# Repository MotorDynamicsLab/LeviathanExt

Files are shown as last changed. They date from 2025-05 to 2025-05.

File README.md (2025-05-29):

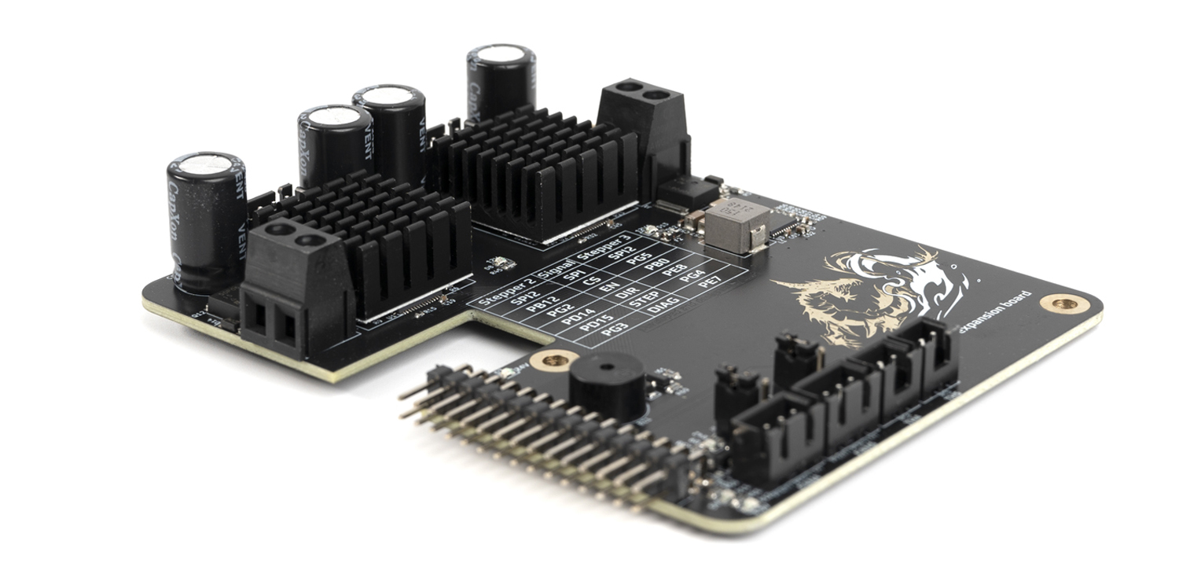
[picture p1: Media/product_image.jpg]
Leviathan_Ext Leviathan Extension


# Leviathan Extension Board

The Leviathan Extension Board is a plug and play PCB that expands the feature set of the original Leviathan controller board. It adds: 

- 2x Integrated TMC5160 stepper drivers. 
- 2x Fan ports with flyback protection, 12V/24V selectable voltage, and tachometer inputs. 
- 2x Thermistor ports with 2k2 ohm pullup resistors. 
- 1x Piezo Buzzer

## Electrical Specifications

| Parameter | Symbol | Min | Typ | Max | Unit | Comments |
| --- | --- | --- | --- | --- | ---- | --- |
| HV Stepper Supply Voltage | V<sub>HV</sub> | 24  | 48  | 55  | V | Supply voltage for the HV stepper drivers |
| Fan Current | I<sub>fan</sub> | | | 0.5 | A | Current rating per fan channel |
| HV Stepper Current | I<sub>hv_mot</sub> | | | 3 | A | Current rating of each TMC5160 stepper driver |

## Creating a Custom Extension PCB

Did you ever want to create your own custom extension board? We have a [template KiCad project](https://github.com/MotorDynamicsLab/Leviathan-Ext-Template) to help get you started.

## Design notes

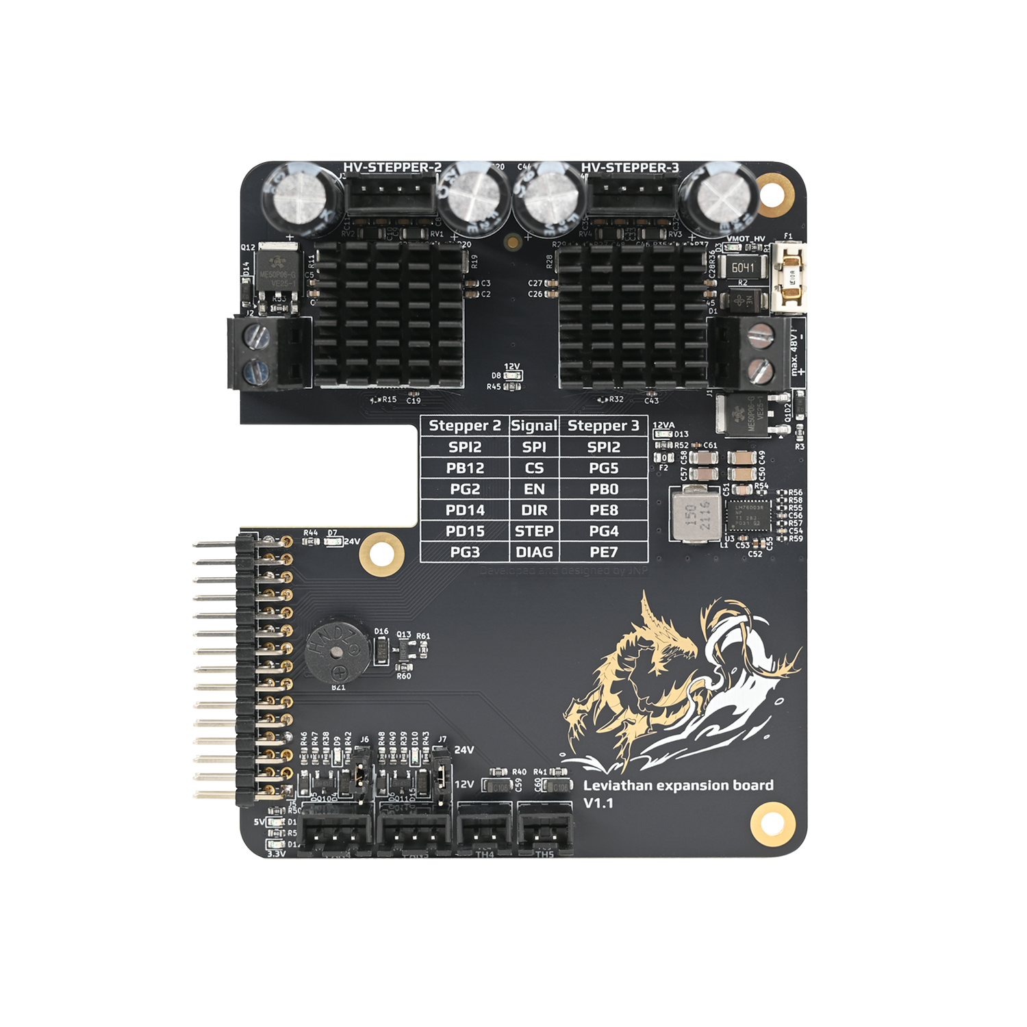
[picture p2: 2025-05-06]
Media/front.jpg

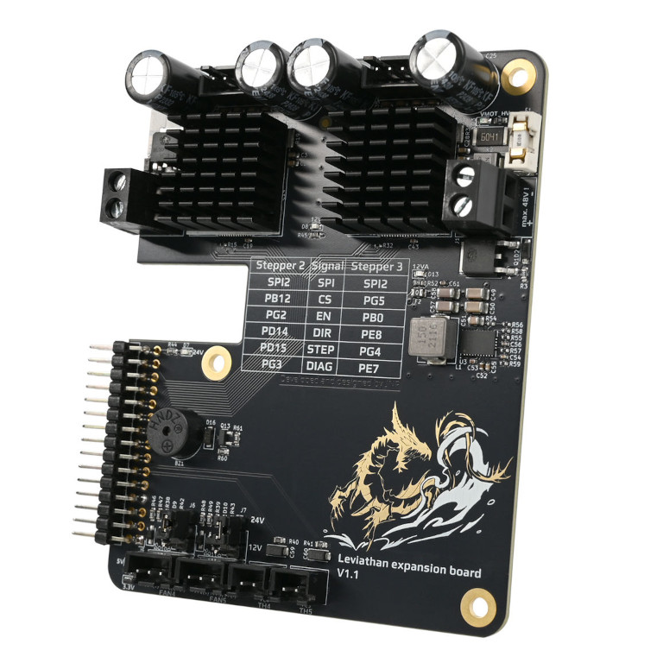
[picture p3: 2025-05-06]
Media/product_img_web.jpg

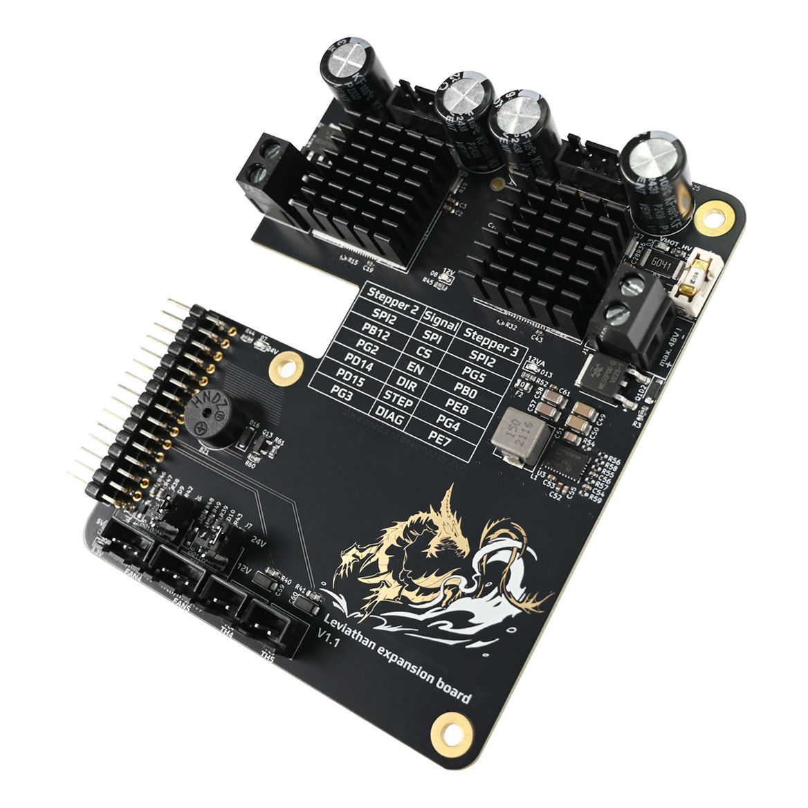
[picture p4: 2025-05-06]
Media/product_img_web1.jpg

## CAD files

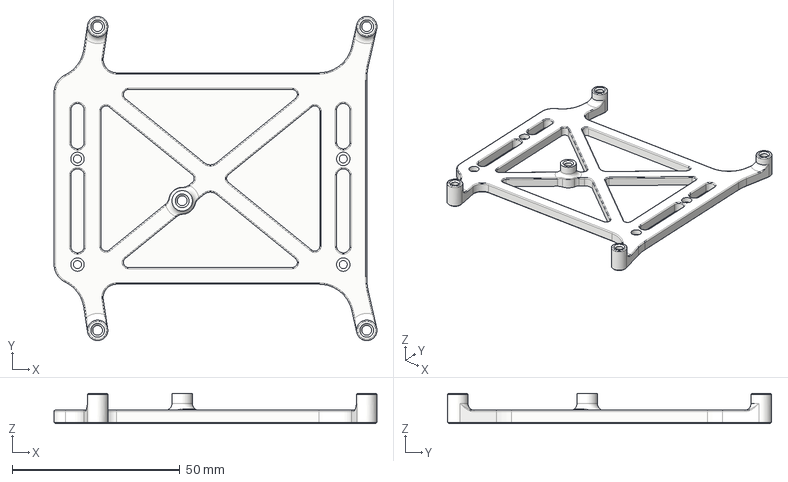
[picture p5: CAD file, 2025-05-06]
STLs/Leviathan Extension Board Bracket.step
96.2 x 96.6 x 9.00 mm

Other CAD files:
STLs/Leviathan Extension Board Bracket.stl

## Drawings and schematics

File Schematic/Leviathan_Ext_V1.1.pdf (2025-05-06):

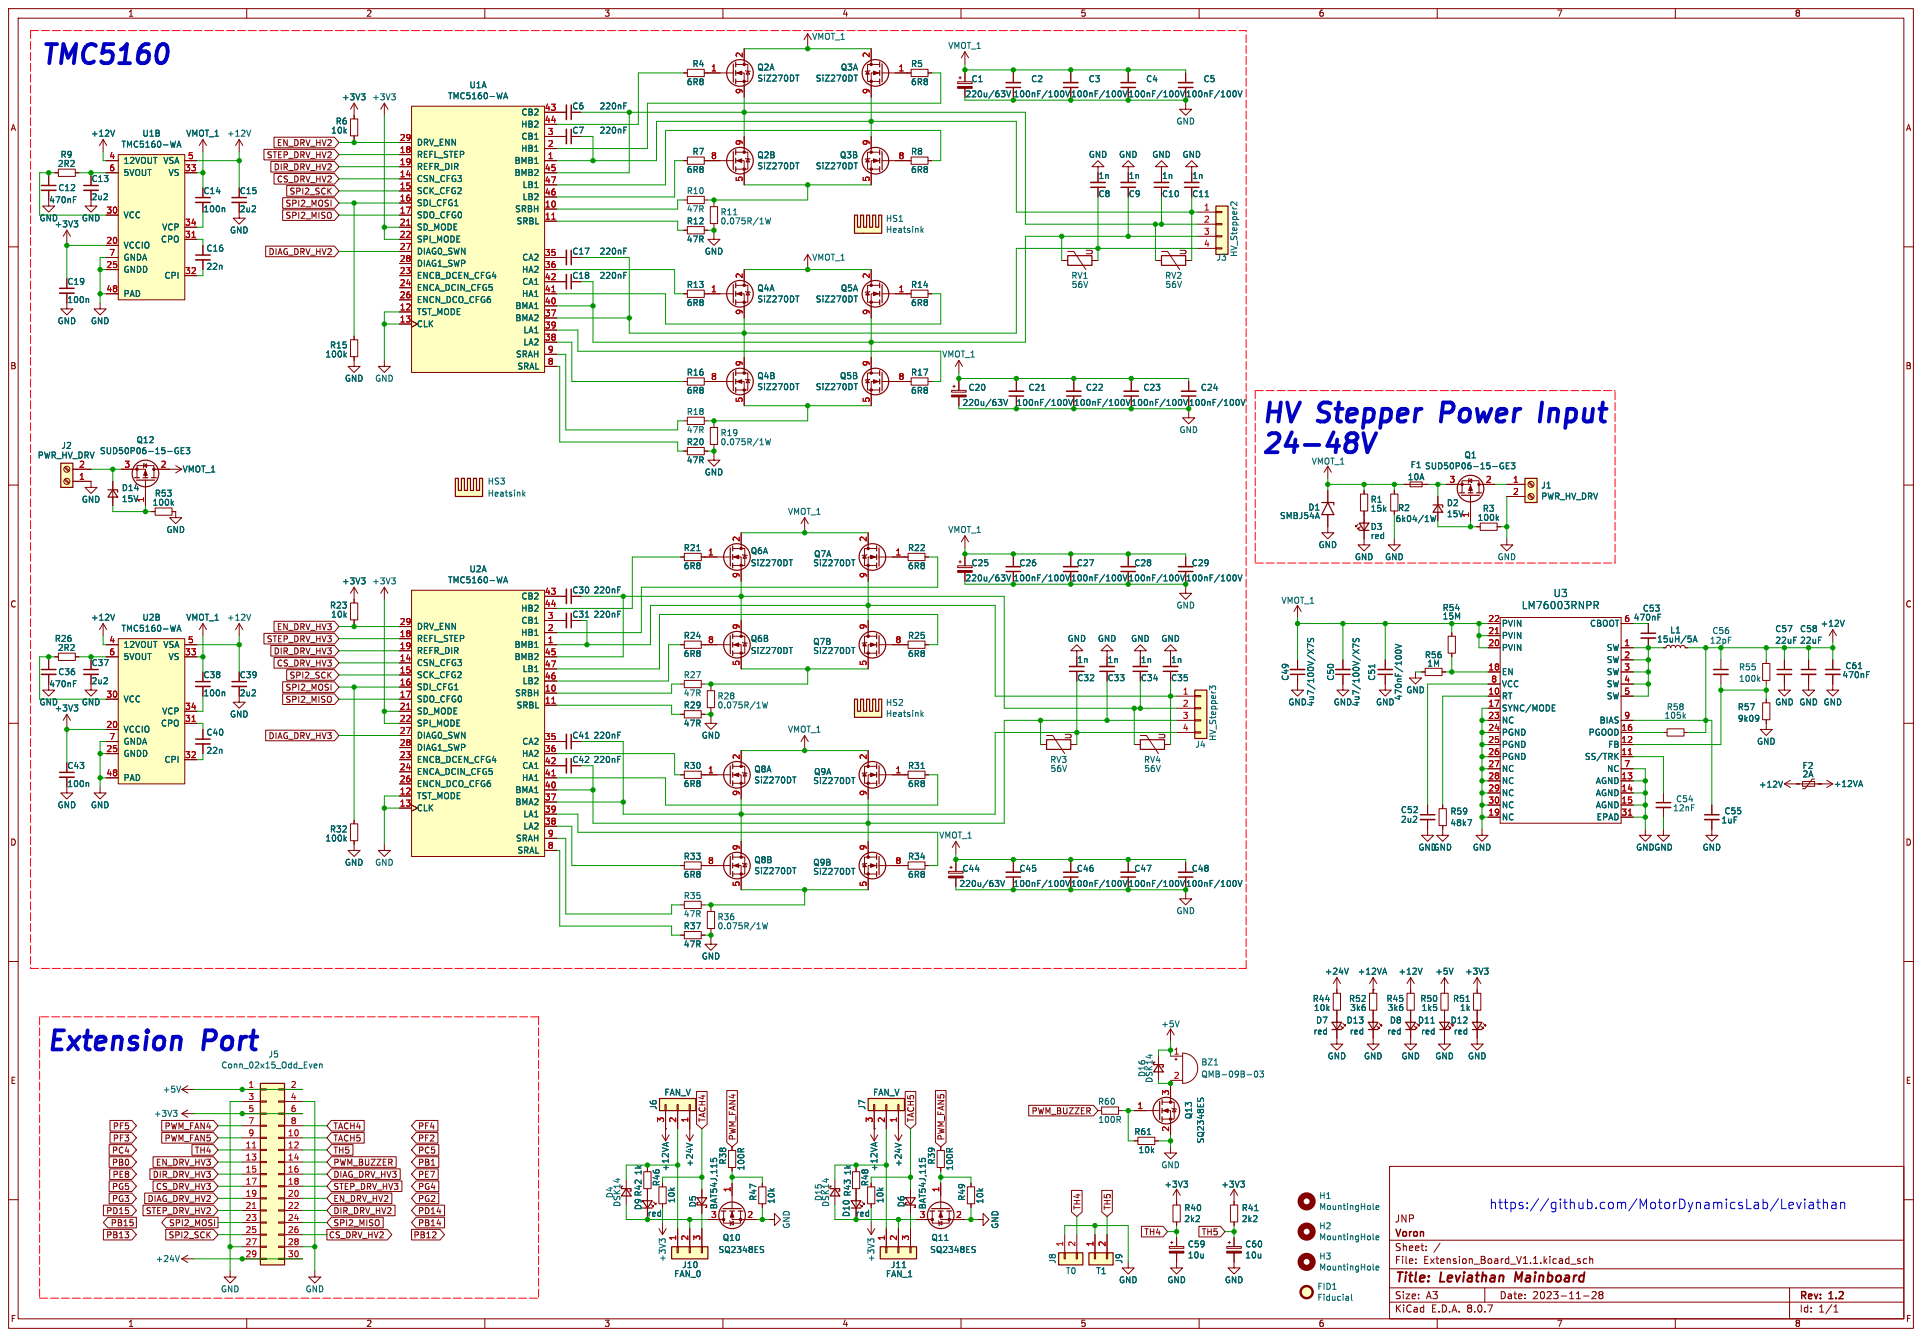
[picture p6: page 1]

https://github.com/MotorDynamicsLab/Leviathan

Id: 1/1 Title: Leviathan Mainboard

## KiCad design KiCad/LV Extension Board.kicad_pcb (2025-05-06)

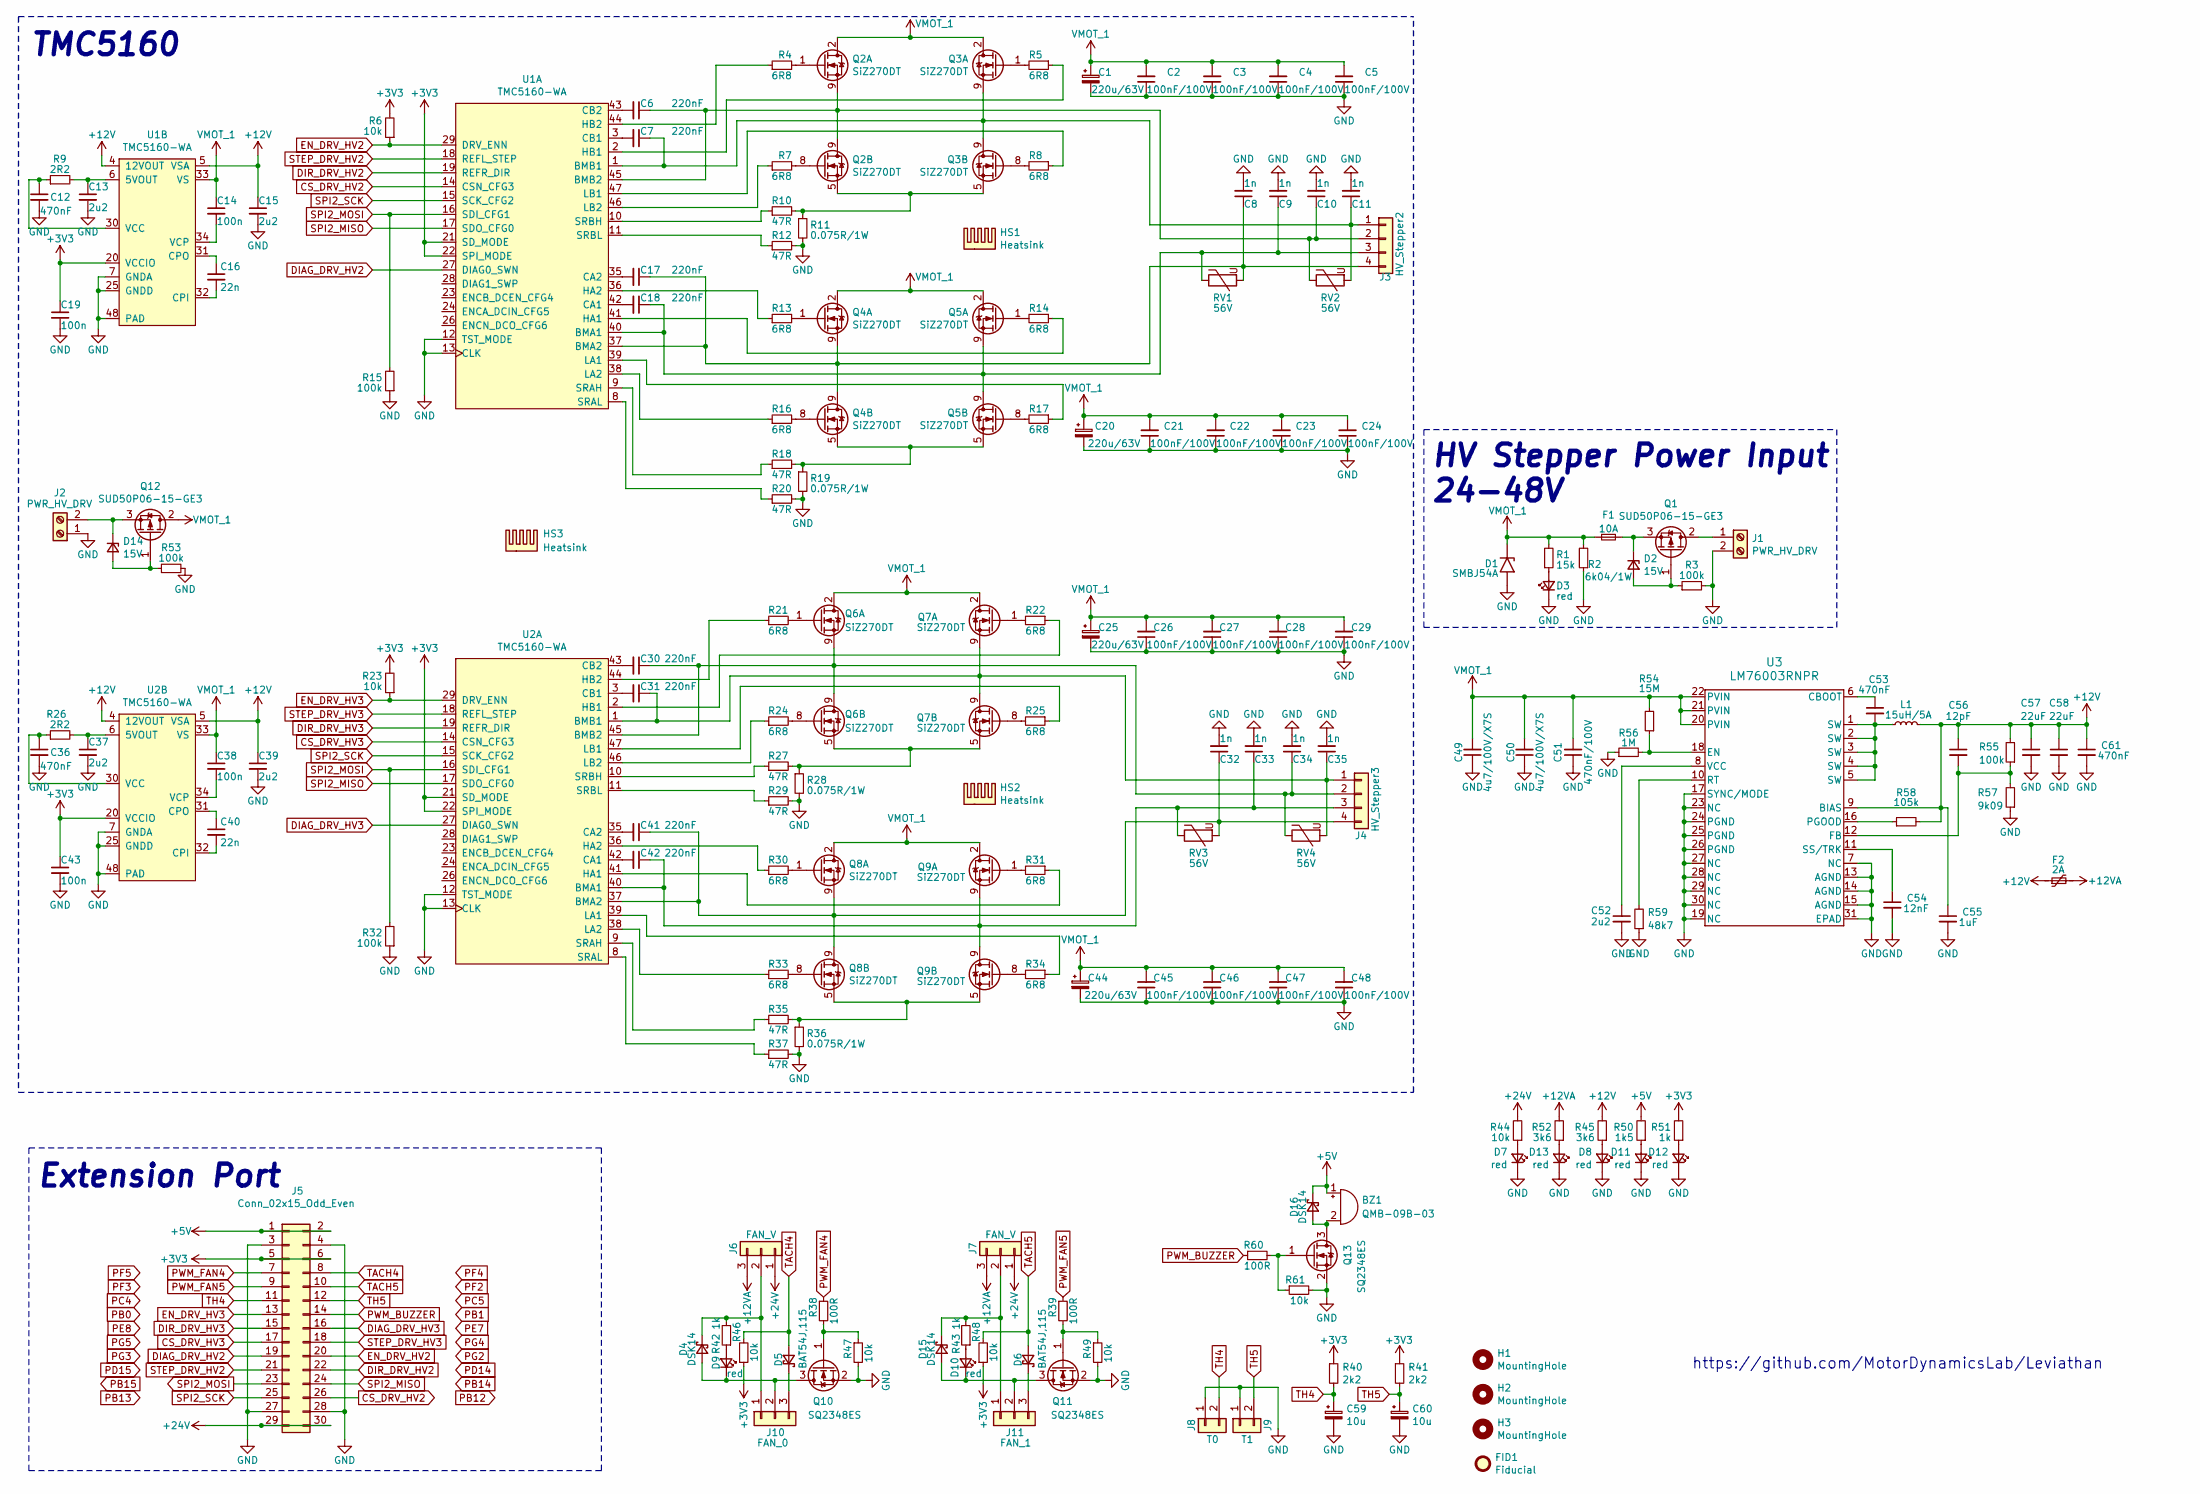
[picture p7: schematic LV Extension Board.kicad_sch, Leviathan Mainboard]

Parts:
BZ1: QMB-09B-03; MagneticBuzzer_PUI_AT-0927-TT-6-R; LCSC C96256
C1, C20, C25, C44: 220u/63V; CP_Radial_D10.0mm_P5.00mm; LCSC C442941
C2, C3, C4, C5, C21, C22, C23, C24, C26, C27, C28, C29, C45, C46, C47, C48: 100nF/100V; C_0603_1608Metric; LCSC C88219
C6, C7, C17, C18, C30, C31, C41, C42: 220nF; C_0603_1608Metric; LCSC C2174190
C8, C9, C10, C11, C32, C33, C34, C35: 1n; C_0603_1608Metric; MFG# 0603B102K101CT; LCSC C77438
C12, C36: 470nF; C_0402_1005Metric; LCSC C961501
C13, C15, C37, C39: 2u2; C_0603_1608Metric; LCSC C99228
C14: 100n; C_0603_1608Metric; LCSC# C116838
C16, C40: 22n; C_0603_1608Metric; LCSC C161234
C19, C43: 100n; C_0402_1005Metric; MFG# C83054; LCSC C83054
C38: 100n; C_0603_1608Metric; LCSC C116838
C49, C50: 4u7/100V/X7S; C_1206_3216Metric; LCSC C237304
C51: 470nF/100V; C_0805_2012Metric; LCSC C97926
C52: 2u2; C_0402_1005Metric; LCSC C2999759
C53, C61: 470nF; C_0402_1005Metric; LCSC C437527
C54: 12nF; C_0402_1005Metric; LCSC C113785
C55: 1uF; C_0402_1005Metric; LCSC C1518208
C56: 12pF; C_0402_1005Metric; LCSC C1547
C57, C58: 22uF; C_1206_3216Metric; LCSC C909845
C59, C60: 10u; CP_EIA-3216-18_Kemet-A; MFG# TC212A106M010B; LCSC# C124849
D1: SMBJ54A; D_SMB; LCSC C353352
D2, D14: 15V; D_SOD-123; LCSC C177014
D3, D7, D8, D9, D10, D11, D12, D13: red; LED_0603_1608Metric; LCSC C434419
D4, D15, D16: DSK14; D_SOD-123F; LCSC C37049
D5, D6: BAT54J,115; D_SOD-323_HandSoldering; LCSC C130415
F1: 10A; Fuseholder_Littelfuse_Nano2_154x; LCSC C206921
F2: 2A; Fuse_0805_2012Metric; LCSC C910824
FID1: Fiducial; Fiducial_1.5mm_Mask3mm
H1, H2, H3: MountingHole; MountingHole_3.2mm_M3_Pad_TopBottom
HS1, HS2: Heatsink; Heatsink_Fischer_ICK_PGA_20x20x10
HS3: Heatsink; M2_Heatsink_55x22x3
J1, J2: PWR_HV_DRV; TerminalBlock_Phoenix_MKDS-1,5-2_1x02_P5.00mm_Horizontal
J3: HV_Stepper2; JST_XH_B4B-XH-A_1x04_P2.50mm_Vertical; LCSC C566013
J4: HV_Stepper3; JST_XH_B4B-XH-A_1x04_P2.50mm_Vertical; LCSC C566013
J5: Conn_02x15_Odd_Even; PinHeader_2x15_P2.54mm_Horizontal
J6, J7: FAN_V; PinHeader_1x03_P2.54mm_Vertical; LCSC C429954
J8: T0; JST_XH_B2B-XH-A_1x02_P2.50mm_Vertical; LCSC C161869
J9: T1; JST_XH_B2B-XH-A_1x02_P2.50mm_Vertical; LCSC C161869
J10: FAN_0; JST_XH_B3B-XH-A_1x03_P2.50mm_Vertical; LCSC C565985
J11: FAN_1; JST_XH_B3B-XH-A_1x03_P2.50mm_Vertical; LCSC C565985
L1: 15uH/5A; L_Chilisin_BMRB00060650; LCSC C2847544
Q1, Q12: SUD50P06-15-GE3; TO-252-2; LCSC C141584
Q2, Q3, Q4, Q5: SiZ270DT; Vishay_PowerPair_3x3S; LCSC C17341509
Q6, Q7, Q8, Q9: SiZ270DT; Vishay_PowerPair_3x3S
Q10, Q11, Q13: SQ2348ES; SOT-23; LCSC C7463653
R1: 15k; R_0603_1608Metric; LCSC C73802
R2: 6k04/1W; R_2512_6332Metric; LCSC C421527
R3, R53: 100k; R_0603_1608Metric; LCSC C14675
R4, R5, R7, R8, R13, R14, R16, R17, R21, R22, R24, R25, R30, R31, R33, R34: 6R8; R_0402_1005Metric; LCSC C227211
R6, R23: 10k; R_0402_1005Metric; LCSC C384294
R9, R26: 2R2; R_0402_1005Metric; LCSC C327251
R10, R12, R18, R20, R27, R29, R35, R37: 47R; R_0402_1005Metric; LCSC C144756
R11, R19, R28, R36: 0.075R/1W; R_2512_6332Metric; LCSC C705611
R15, R32: 100k; R_0402_1005Metric; LCSC C132374
R38, R39, R60: 100R; R_0603_1608Metric; LCSC C327825
R40, R41: 2k2; R_0603_1608Metric; LCSC C445630
R42, R43, R51: 1k; R_0603_1608Metric; LCSC C14676
R44: 10k; R_0603_1608Metric; LCSC# C384294
R45, R52: 3k6; R_0603_1608Metric; LCSC C103578
R46, R47, R48, R49, R61: 10k; R_0603_1608Metric; LCSC C384294
R50: 1k5; R_0603_1608Metric; LCSC C22843
R54: 15M; R_0402_1005Metric; LCSC C7422144
R55: 100k; R_0402_1005Metric; LCSC C60491
R56: 1M; R_0402_1005Metric; LCSC C26083
R57: 9k09; R_0402_1005Metric; LCSC C11549
R58: 105k; R_0402_1005Metric; LCSC C171671
R59: 48k7; R_0402_1005Metric; LCSC C103068
RV1, RV2, RV3, RV4: 56V; R_1206_3216Metric; LCSC C2935553
U1, U2: TMC5160-WA; QFN-56-1EP_8x8mm_P0.5mm_EP6.25x6.25mm_ThermalVias_TMC; LCSC C1161714
U3: LM76003RNPR; Texas_RNP30; LCSC C470958

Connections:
+3V3: C19.1, C43.1, J5.5, J5.6, R6.2, R23.2, R40.1, R41.1, R46.1, R48.1, R51.2, U1.20 (VCCIO), U1.21 (SD_MODE), U1.22 (SPI_MODE), U2.20 (VCCIO), U2.21 (SD_MODE), U2.22 (SPI_MODE)
+5V: BZ1.1 (+), D16.1 (K), J5.1, J5.2, R50.2
+12V: C15.1, C39.1, C55.1, C56.1, C57.1, C58.1, C61.1, F2.1, L1.2, R45.2, R55.2, R58.2, U1.4 (12VOUT), U1.5 (VSA), U2.4 (12VOUT), U2.5 (VSA), U3.9 (BIAS)
+12VA: F2.2, J6.3, J7.3, R52.2
+24V: J5.29, J5.30, J6.1, J7.1, R44.2
CS_DRV_HV2: J5.26, U1.14 (CSN_CFG3)
CS_DRV_HV3: J5.17, U2.14 (CSN_CFG3)
DIAG_DRV_HV2: J5.19, U1.27 (DIAG0_SWN)
DIAG_DRV_HV3: J5.16, U2.27 (DIAG0_SWN)
DIR_DRV_HV2: J5.22, U1.19 (REFR_DIR)
DIR_DRV_HV3: J5.15, U2.19 (REFR_DIR)
EN_DRV_HV2: J5.20, R6.1, U1.29 (DRV_ENN)
EN_DRV_HV3: J5.13, R23.1, U2.29 (DRV_ENN)
GND: C1.2, C2.1, C3.1, C4.1, C5.1, C8.2, C9.2, C10.2, C11.2, C12.2, C13.2, C15.2, C19.2, C20.2, C21.1, C22.1, C23.1, C24.1, C25.2, C26.1, C27.1, C28.1, C29.1, C32.2, C33.2, C34.2, C35.2, C36.2, C37.2, C39.2, C43.2, C44.2, C45.1, C46.1, C47.1, C48.1, C49.1, C50.1, C51.1, C52.2, C54.2, C55.2, C57.2, C58.2, C59.2, C60.2, C61.2, D1.2 (A2), D3.1 (K), D7.1 (K), D8.1 (K), D11.1 (K), D12.1 (K), D13.1 (K), J1.2, J2.1, J5.3, J5.4, J5.27, J5.28, J8.1, J9.1, Q10.2 (S), Q11.2 (S), Q13.2 (S), R2.1, R3.2, R11.2, R12.2, R15.1, R19.2, R20.2, R28.2, R29.2, R32.1, R36.2, R37.2, R47.2, R49.2, R53.2, R56.1, R57.1, R59.1, R61.2, U1.7 (GNDA), U1.12 (TST_MODE), U1.13 (CLK), U1.25 (GNDD), U1.48 (PAD), U2.7 (GNDA), U2.12 (TST_MODE), U2.13 (CLK), U2.25 (GNDD), U2.48 (PAD), U3.7 (NC), U3.13 (AGND), U3.14 (AGND), U3.15 (AGND), U3.17 (SYNC/MODE), U3.19 (NC), U3.23 (NC), U3.24 (PGND), U3.25 (PGND), U3.26 (PGND), U3.27 (NC), U3.28 (NC), U3.29 (NC), U3.30 (NC), U3.31 (EPAD)
unnamed: BZ1.2 (-), D16.2 (A), Q13.3 (D)
unnamed: C53.2, L1.1, U3.1 (SW), U3.2 (SW), U3.3 (SW), U3.4 (SW), U3.5 (SW)
unnamed: D2.2 (A), Q1.1 (G), R3.1
unnamed: D2.1 (K), F1.2, Q1.3 (S)
unnamed: D3.2 (A), R1.1
unnamed: D4.2 (A), D9.1 (K), J10.2, Q10.3 (D)
unnamed: D4.1 (K), J6.2, J10.1, R42.2
unnamed: D5.1 (K), J10.3
unnamed: D6.1 (K), J11.3
unnamed: D7.2 (A), R44.1
unnamed: D8.2 (A), R45.1
unnamed: D9.2 (A), R42.1
unnamed: D10.2 (A), R43.1
unnamed: D10.1 (K), D15.2 (A), J11.2, Q11.3 (D)
unnamed: D11.2 (A), R50.1
unnamed: D12.2 (A), R51.1
unnamed: D13.2 (A), R52.1
unnamed: D14.2 (A), Q12.1 (G), R53.1
unnamed: D14.1 (K), J2.2, Q12.3 (S)
unnamed: D15.1 (K), J7.2, J11.1, R43.2
unnamed: J1.1, Q1.2 (D)
unnamed: C7.1, C11.1, J3.1, Q3.9 (S), RV2.2, U1.1 (BMB1)
unnamed: C6.1, C10.1, J3.2, Q2.9 (S), RV2.1, U1.45 (BMB2)
unnamed: C9.1, C18.1, J3.3, Q5.9 (S), RV1.1, U1.40 (BMA1)
unnamed: C8.1, C17.1, J3.4, Q4.9 (S), RV1.2, U1.37 (BMA2)
unnamed: C31.1, C35.1, J4.1, Q7.9 (S), RV4.2, U2.1 (BMB1)
unnamed: C30.1, C34.1, J4.2, Q6.9 (S), RV4.1, U2.45 (BMB2)
unnamed: C33.1, C42.1, J4.3, Q9.9 (S), RV3.1, U2.40 (BMA1)
unnamed: C32.1, C41.1, J4.4, Q8.9 (S), RV3.2, U2.37 (BMA2)
unnamed: Q2.1 (G), R4.2
unnamed: Q2.8 (G), R7.2
unnamed: Q2.5 (S), Q3.5 (S), R10.2, R11.1
unnamed: Q3.1 (G), R5.2
unnamed: Q3.8 (G), R8.2
unnamed: Q4.1 (G), R13.2
unnamed: Q4.8 (G), R16.2
unnamed: Q4.5 (S), Q5.5 (S), R18.2, R19.1
unnamed: Q5.1 (G), R14.2
unnamed: Q5.8 (G), R17.2
unnamed: Q6.1 (G), R21.2
unnamed: Q6.8 (G), R24.2
unnamed: Q6.5 (S), Q7.5 (S), R27.2, R28.1
unnamed: Q7.1 (G), R22.2
unnamed: Q7.8 (G), R25.2
unnamed: Q8.1 (G), R30.2
unnamed: Q8.8 (G), R33.2
unnamed: Q8.5 (S), Q9.5 (S), R35.2, R36.1
unnamed: Q9.1 (G), R31.2
unnamed: Q9.8 (G), R34.2
unnamed: Q10.1 (G), R38.2, R47.1
unnamed: Q11.1 (G), R39.2, R49.1
unnamed: Q13.1 (G), R60.2, R61.1
unnamed: C18.2, U1.42 (CA1)
unnamed: C17.2, U1.35 (CA2)
unnamed: C7.2, U1.3 (CB1)
unnamed: C6.2, U1.43 (CB2)
unnamed: R14.1, U1.41 (HA1)
unnamed: R13.1, U1.36 (HA2)
unnamed: R5.1, U1.2 (HB1)
unnamed: R4.1, U1.44 (HB2)
unnamed: R17.1, U1.39 (LA1)
unnamed: R16.1, U1.38 (LA2)
unnamed: R8.1, U1.47 (LB1)
unnamed: R7.1, U1.46 (LB2)
unnamed: R18.1, U1.9 (SRAH)
unnamed: R20.1, U1.8 (SRAL)
unnamed: R10.1, U1.10 (SRBH)
unnamed: R12.1, U1.11 (SRBL)
unnamed: C13.1, R9.2, U1.6 (5VOUT)
unnamed: C16.2, U1.32 (CPI)
unnamed: C16.1, U1.31 (CPO)
unnamed: C12.1, R9.1, U1.30 (VCC)
unnamed: C14.2, U1.34 (VCP)
unnamed: C42.2, U2.42 (CA1)
unnamed: C41.2, U2.35 (CA2)
unnamed: C31.2, U2.3 (CB1)
unnamed: C30.2, U2.43 (CB2)
unnamed: R31.1, U2.41 (HA1)
unnamed: R30.1, U2.36 (HA2)
unnamed: R22.1, U2.2 (HB1)
unnamed: R21.1, U2.44 (HB2)
unnamed: R34.1, U2.39 (LA1)
unnamed: R33.1, U2.38 (LA2)
unnamed: R25.1, U2.47 (LB1)
unnamed: R24.1, U2.46 (LB2)
unnamed: R35.1, U2.9 (SRAH)
unnamed: R37.1, U2.8 (SRAL)
unnamed: R27.1, U2.10 (SRBH)
unnamed: R29.1, U2.11 (SRBL)
unnamed: C37.1, R26.2, U2.6 (5VOUT)
unnamed: C40.2, U2.32 (CPI)
unnamed: C40.1, U2.31 (CPO)
unnamed: C36.1, R26.1, U2.30 (VCC)
unnamed: C38.2, U2.34 (VCP)
unnamed: C53.1, U3.6 (CBOOT)
unnamed: R54.1, R56.2, U3.18 (EN)
unnamed: C56.2, R55.1, R57.2, U3.12 (FB)
unnamed: R58.1, U3.16 (PGOOD)
unnamed: R59.2, U3.10 (RT)
unnamed: C54.1, U3.11 (SS/TRK)
unnamed: C52.1, U3.8 (VCC)
PWM_BUZZER: J5.14, R60.1
PWM_FAN4: J5.7, R38.1
PWM_FAN5: J5.9, R39.1
SPI2_MISO: J5.24, U1.17 (SDO_CFG0), U2.17 (SDO_CFG0)
SPI2_MOSI: J5.23, R15.2, R32.2, U1.16 (SDI_CFG1), U2.16 (SDI_CFG1)
SPI2_SCK: J5.25, U1.15 (SCK_CFG2), U2.15 (SCK_CFG2)
STEP_DRV_HV2: J5.21, U1.18 (REFL_STEP)
STEP_DRV_HV3: J5.18, U2.18 (REFL_STEP)
TACH4: D5.2 (A), J5.8, R46.2
TACH5: D6.2 (A), J5.10, R48.2
TH4: C59.1, J5.11, J8.2, R40.2
TH5: C60.1, J5.12, J9.2, R41.2
VMOT_1: C1.1, C2.2, C3.2, C4.2, C5.2, C14.1, C20.1, C21.2, C22.2, C23.2, C24.2, C25.1, C26.2, C27.2, C28.2, C29.2, C38.1, C44.1, C45.2, C46.2, C47.2, C48.2, C49.2, C50.2, C51.2, D1.1 (A1), F1.1, Q2.2 (D), Q3.2 (D), Q4.2 (D), Q5.2 (D), Q6.2 (D), Q7.2 (D), Q8.2 (D), Q9.2 (D), Q12.2 (D), R1.2, R2.2, R54.2, U1.33 (VS), U2.33 (VS), U3.20 (PVIN), U3.21 (PVIN), U3.22 (PVIN)

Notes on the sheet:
Extension Port
HV Stepper Power Input 24-48V
https://github.com/MotorDynamicsLab/Leviathan
TMC5160

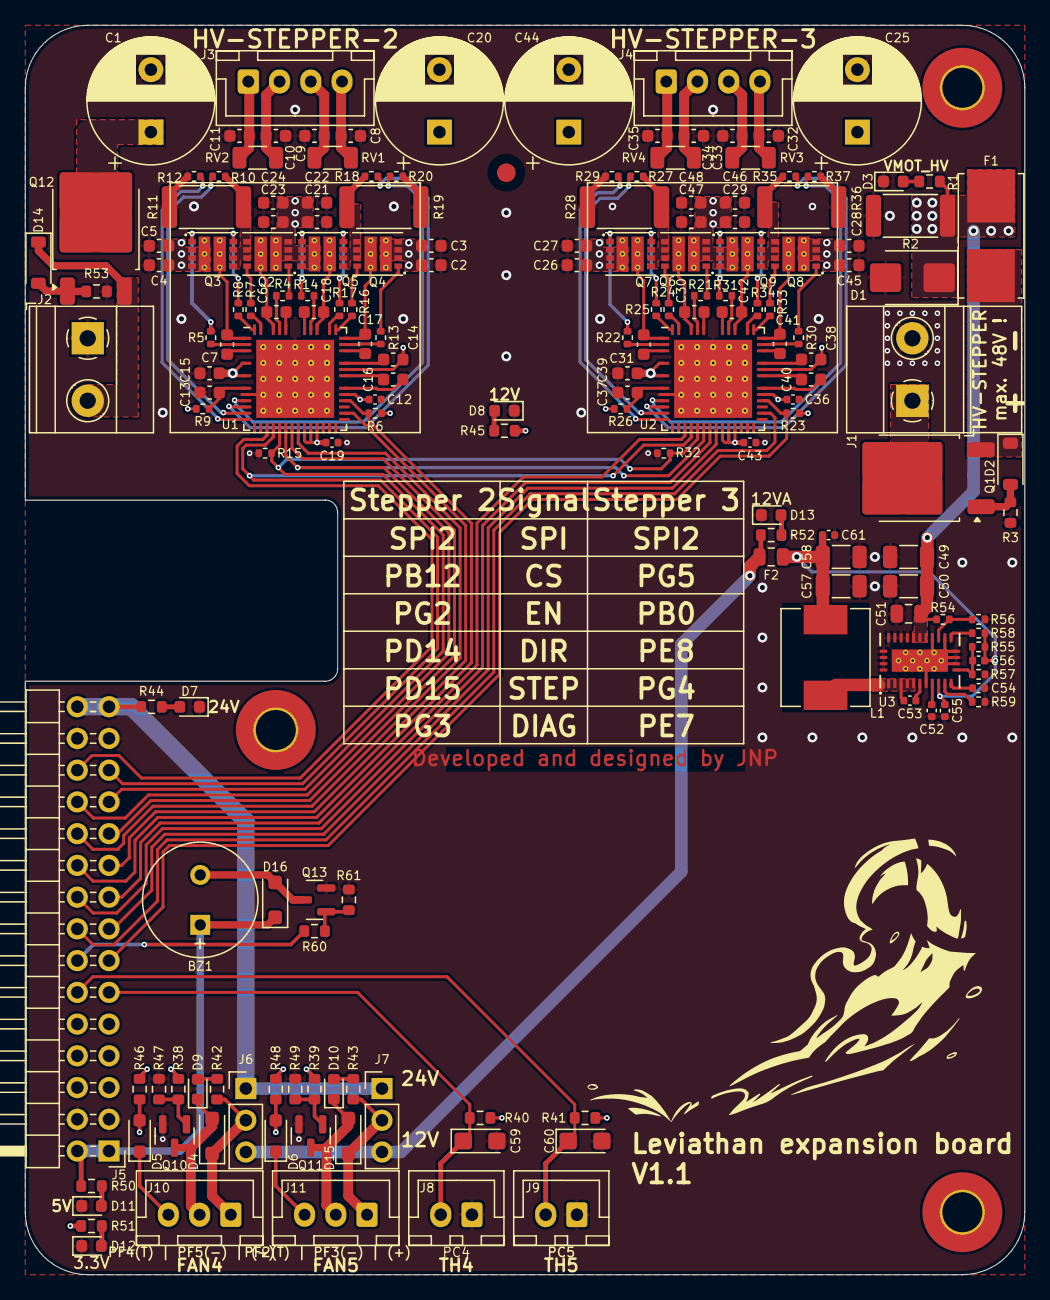
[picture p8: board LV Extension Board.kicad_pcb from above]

Board: 4 copper layers, 80.0 x 100.0 mm, 180 parts (1 on the bottom side), 128 nets.

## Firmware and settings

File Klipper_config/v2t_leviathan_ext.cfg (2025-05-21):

# This file contains pin mappings for the Leviathan Extension Board
# This file can either be included in printer.cfg or its content can be copy pasted into another config file.

## Leviathan Extension Board config

## *** THINGS TO CHANGE/CHECK: ***
## Motor settings                 		[stepper_x1] [stepper_y1] sections
## Fan types                            [fan_generic] sections - See https://www.klipper3d.org/Config_Reference.html?#fans for fan types
## Thermistor types                     [temperature_sensor] sections - See https://www.klipper3d.org/Config_Reference.html#common-thermistors for common thermistor types

#####################################################################
#   X/Y Stepper Settings
#####################################################################

## Tips for configuring your machine for All Wheel Drive (AWD)
## - In a typical AWD configuration, we have two sets of two motors, each set drives a direction (usually diagonal in corexy)
## - Within a set, the motors are typically placed diagonally. e.g.: stepper_x and stepper_x1 are in the same set, and physically located diagonal to each other
## - If the front motors are installed upside down and the rear motors are right side up, then the dir pins within the same set should be opposite sign (! in the config)
## - Make sure the rotation distance/microsteps/full_steps_per_rotation are the same for all sets 
## - rotation_distance = motor_pulley_teeth_count * belt_teeth_pitch (for 2GT the pitch is 2)

##  B1 Stepper - Front Right
##  Connected to HV STEPPER 2
[stepper_x1]
step_pin: PD15
dir_pin: PD14
enable_pin: !PG2
rotation_distance: 40
microsteps: 32
full_steps_per_rotation:400  #set to 200 for 1.8 degree stepper

[tmc5160 stepper_x1]
cs_pin: PB12
spi_bus: spi2
#diag0_pin: ^!PG3
interpolate: false
run_current: 0.8
sense_resistor: 0.075
stealthchop_threshold: 0

##  A1 Stepper - Front Left
##  Connected to HV STEPPER 3
[stepper_y1]
step_pin: PG4
dir_pin: PE8
enable_pin: !PB0
rotation_distance: 40
microsteps: 32
full_steps_per_rotation:400  #set to 200 for 1.8 degree stepper

[tmc5160 stepper_y1]
cs_pin: PG5
spi_bus: spi2
#diag0_pin: ^!PE7
interpolate: false
run_current: 0.8
sense_resistor: 0.075
stealthchop_threshold: 0


#####################################################################
#   Fan Control
#####################################################################

# ##  Change fan type as needed, e.g. heater_fan, temperature_fan 
# [fan_generic fan4]
# ##  Generic Fan - FAN4
# pin: PF5
# tachometer_pin: PF4

# ##  Change fan type as needed, e.g. heater_fan, temperature_fan 
# [fan_generic fan5]
# ##  Generic Fan - FAN5
# pin: PF3
# tachometer_pin: PF2

#####################################################################
#   Thermistors
#####################################################################

# [temperature_sensor therm4]
# ##  Temperature Sensor - TH4
# ## Check what thermistor type you have. See https://www.klipper3d.org/Config_Reference.html#common-thermistors for common thermistor types.
# sensor_type: ATC Semitec 104NT-4-R025H42G
# sensor_pin: PC4
# min_temp: 0
# max_temp: 300
# pullup_resistor: 2200

# [temperature_sensor therm5]
# ##  Temperature Sensor - TH5
# ## Check what thermistor type you have. See https://www.klipper3d.org/Config_Reference.html#common-thermistors for common thermistor types.
# sensor_type: ATC Semitec 104NT-4-R025H42G
# sensor_pin: PC5
# min_temp: 0
# max_temp: 300
# pullup_resistor: 2200

#####################################################################
#   Buzzer
#####################################################################

[pwm_cycle_time _beeper]
## Passive Buzzer - varying cycle time varies the pitch
pin: PB1
shutdown_value: 0
value: 0

#####################################################################
#   Macros
#####################################################################

## Emits an audible tone, use in conjunction with a passive buzzer to create beeps of different pitch and durations
## Original code from: https://github.com/rootiest/zippy-klipper_config/blob/master/macros/M300.cfg
## Script that converts MIDI files to M300 gcode: https://alexyu132.github.io/midi-m300/
[gcode_macro M300]
gcode:
    {% set S = params.S|default(1000)|int %} ; S sets the tone frequency
    {% set P = params.P|default(100)|int %} ; P sets the tone duration
    {% set L = 0.5 %} ; L varies the PWM on time, close to 0 or 1 the tone gets a bit quieter. 0.5 is a symmetric waveform
    {% if S <= 0 %} ; dont divide through zero
        {% set F = 1 %}
        {% set L = 0 %}
    {% elif S >= 10000 %} ;max frequency set to 10kHz
        {% set F = 0 %}
    {% else %}
        {% set F = 1/S %} ;convert frequency to seconds
    {% endif %}
    SET_PIN PIN=_beeper VALUE={L} CYCLE_TIME={F} ;Play tone
    G4 P{P} ;tone duration
    SET_PIN PIN=_beeper VALUE=0

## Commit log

2025-05-06 add printed bracket files as well as photo images
    [Leviathan Extension Board Bracket.step, Leviathan Extension Board Bracket.stl]
2025-05-06 add schematics
2025-05-06 add KiCAD source
    [LV Extension Board.kicad_pcb, LV Extension Board.kicad_sch]
2025-05-07 add klipper config
    [v2t_leviathan_ext.cfg]
2025-05-07 add KiCad/PRODUCTION directory to gitignore
2025-05-21 update buzzer config from normal output_pin to pwm_cycle_time
    [v2t_leviathan_ext.cfg]
